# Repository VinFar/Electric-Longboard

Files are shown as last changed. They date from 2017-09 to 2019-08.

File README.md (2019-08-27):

# Self-Build electric mountain- and longboard with VESC and BLDC motor

##### Pressreport: https://www.fh-muenster.de/hochschule/aktuelles/pressemitteilungen.php?pmid=7254

This is a small Repo about my selfbuild electric mountain- and longboard, which I began to build in 2016 and 2019.
These are never ending projects, cause I will always come up with new ideas.

## Mountainboard
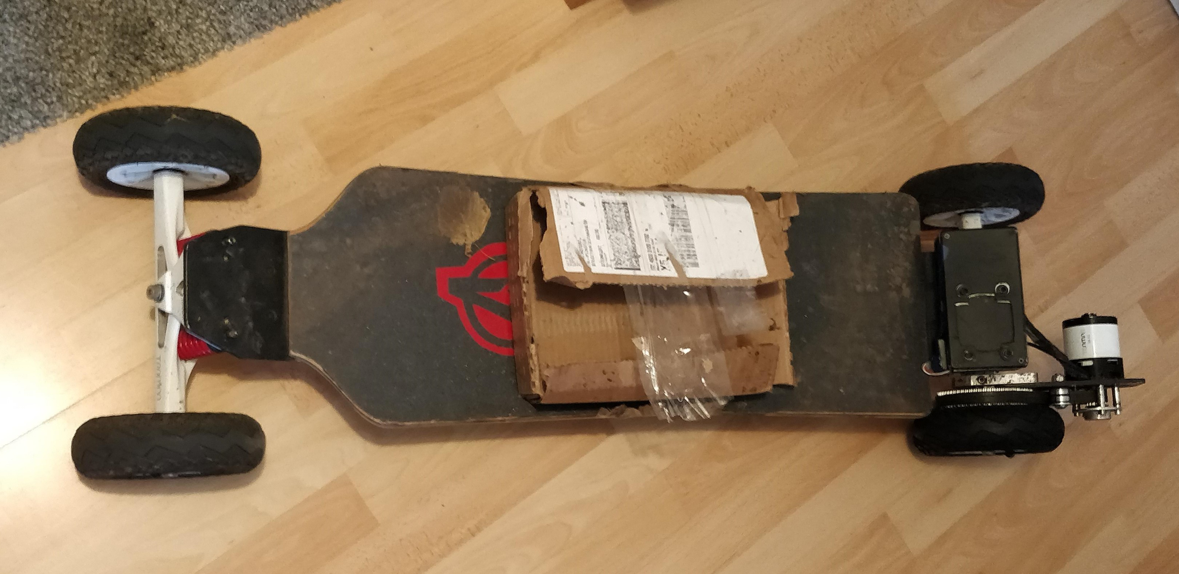
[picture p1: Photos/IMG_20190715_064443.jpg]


The longboard has been running very well for some time now and it's a lot of fun to ride.
But the small wheels (70mm diameter) are annoying and dangerous, because you have to pay attention to all medium sized stones and edges on the road, which will make the rides exhausting. Due of this and also because I was looking for a new challenge, I started building a mountainboard in May 2019.
This must have the following improvements:

- big pneumatic tires (at least 130mm in diameter)
- higher range (at least 30 km)
- newer version of the VESC
- USB-C PD charging capability
- 12S4P Li-ion battery pack

The first rough prototype of this is shown in the picture above. The box in the middle is a temporary battery box for testing.
At the moment (27.08.19) it has pneumatic tires with a diameter of 160mm, a range of about 35km  with ~600Wh 12S2P Lipos and VESC 6 with Bluetooth module.

Another thing that bothered me with the first longboard, was that I always had to take a 12V PSU and a Lipo charger with me in order to charge the batteries.
So for the Mountainboard i came up with the idea of charging the batteries over a [60W - 100W USB C Power Delivery power supply](https://www.voelkner.de/products/1055964/LVSUN-80W-USB-C-QC3.0-LS-Q5U-PD-USB-Ladestation-Steckdose-Ausgangsstrom-max.-17000mA-5-x-USB-3.0-Buchse-A-USB-C-Buchse-USB.h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). On awesome feature of USB C is that it can deliver up to [100W over the small USB-C plug](https://en.wikipedia.org/wiki/USB-C#USB_Power_Delivery) (20V and 5A).
I want to use this in combination with a [50V boost converter](https://www.droking.com/dc-boost-converter-power-supply-module-adjustable-regulator-dc-10v-40v-to-10-50v-6a-step-up-converter-dc-12v-24v-cc-cv-voltage-regulator-boar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) and the open source BMS [DieBieMS](https://github.com/DieBieEngineering/DieBieMS) to have to ability to charge it on every socket.

The 12S4P Li-ion battery pack will be mounted beneath the deck in the form of a modular system, which is shown below.
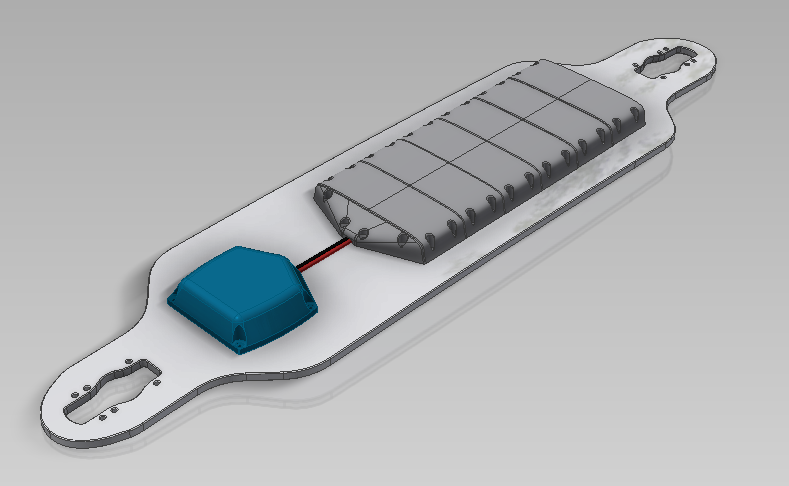
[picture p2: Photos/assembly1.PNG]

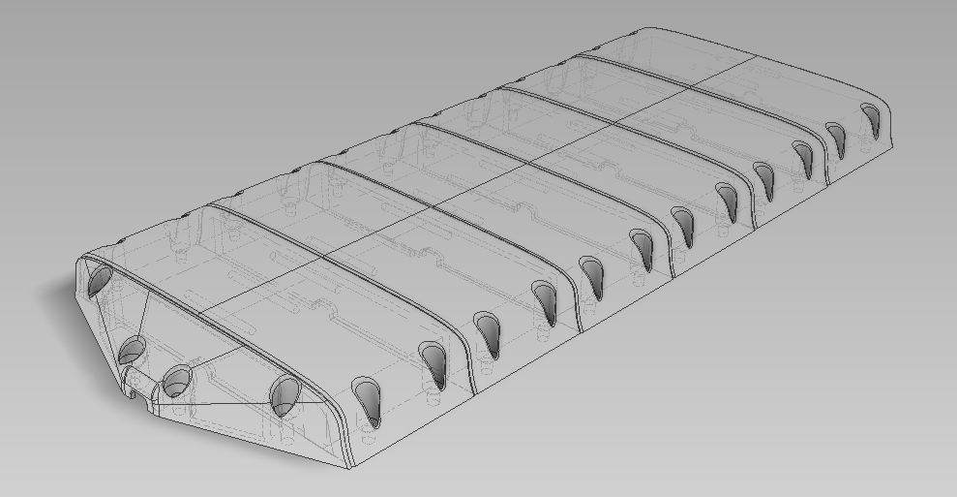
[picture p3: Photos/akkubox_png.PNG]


In every battery tray there is space for a 2S3P/3S2P/1S6P/6S1P battery pack. This trays are then connected in series to raise the voltage and/or the capacity. The BMS, the converter and the VESC will sit in the blue housing at the end of the mountainboard.

The first test ride with the this board were awesome. It runs so much better on all terrains, so you don't have to worry about stones and bumps any more. Even on uneven tracks like in a forest or on grass it runs good.

In the future I will get a second motor to also drive the second tire and to have more torque (at the moment the power is ok, but could definitly be more).

## Longboard
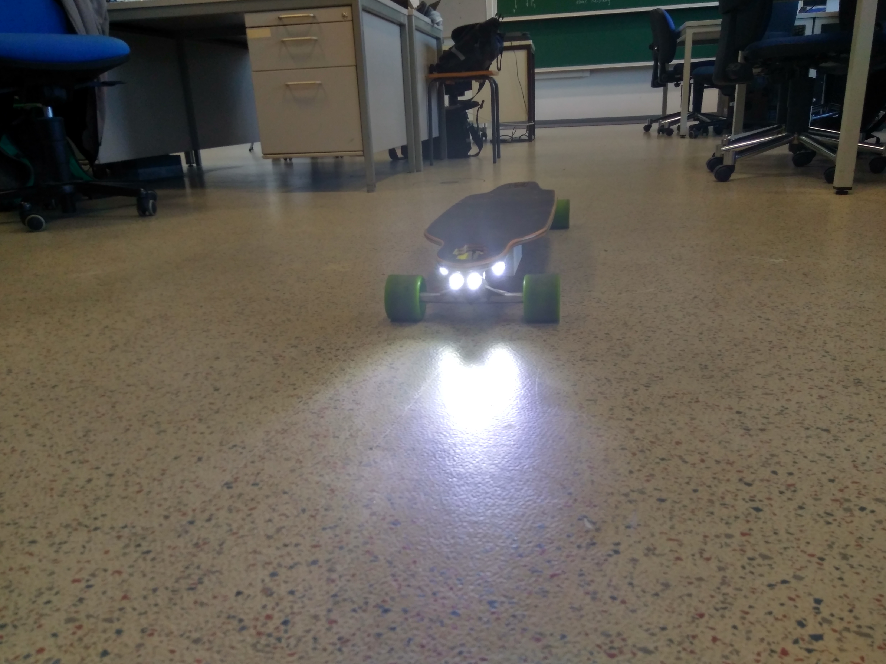
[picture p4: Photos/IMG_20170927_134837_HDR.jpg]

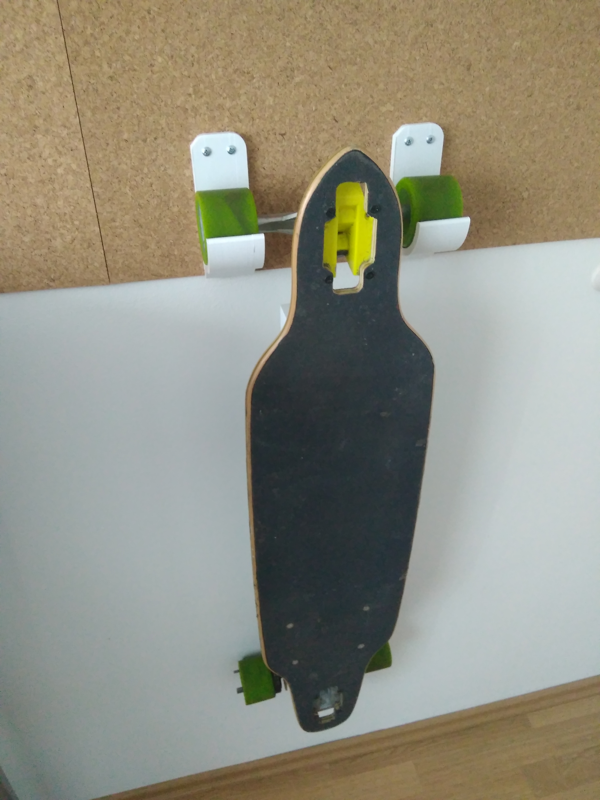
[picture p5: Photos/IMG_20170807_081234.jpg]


#### ToDo's:
* Backlight with Brakelight
* [Failsafe Function with Rubberband](https://www.svb.de/de/sicherheits-schalter.html)
  -If you jump off the board, let the board make a full brake

#### Not-ToDo's (already done):
* Cleaner Cable Managment
  - XT-60 Box
* Built cases
  - VESC-Case
  - CC converter case
  - Battery case
* Better Motorplate
  - 3mm stainless steel
* Changed Transmitter Case
  - [Baby Buffalo](https://www.thingiverse.com/thing:1810252)
* [LED-Headlight](https://github.com/VinFar/Electric-Longboard/tree/master/Inventor%20Files/LED-Headlight)

For the motor I choose [this BLDC Motor](http://www.hellray.de/shop/#!/eSk8-de-Motor-esk8-6354-200kV-2-2KW-mit-Sensoren/p/65758944/category=15255004).
It is recommend for 2,2kW, but due to sufficient cooling it can be powered with up to ~3.2kW (~40V with 80A max, efficiency ignored).

For the ESC I went with the aweseome [VESC 4](http://vedder.se/2015/01/vesc-open-source-esc/).

As Batteries two 5s LiPos are used, which are connected in series to get a voltage of up to 42V.
They have 5Ah each, so a total energy of around 200Wh can be consumed, which is enough 10-15 km depending on the driving speed.

For the Communication between the VESC and the driver, I got a [GT2B](https://www.google.de/search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), which i then put into a [3D printed housing](https://www.thingiverse.com/thing:1810252) to get a small and ergonomic remote.

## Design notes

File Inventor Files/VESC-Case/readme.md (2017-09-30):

# Nice looking Case for VESC and other Components

This is is stylish Case for the VESC and other Compoments like Capacitors, Buck-Converters,Receiver etc...
It is about 35mm in height, therefore it looks very slim under the board.
For this Case I also scanned the Outlines from the bottom part of the Longboard, to make it look like a part of the Board.

I uploaded a [Clean Version](https://github.com/VinFar/Electric-Longboard/blob/master/Inventor%20Files/VESC-Case/Clean_Version_2.stl), in which is only the Case without any cutouts or holes, so you can edit it for yourself.
Also there is a ["USB Version"](https://github.com/VinFar/Electric-Longboard/blob/master/Inventor%20Files/VESC-Case/USB_Version_2.stl),
where i made some cutouts and holes for switches, Powercables, USB-Output etc...

Clean Version(no cutouts): [Clean_Version_2.stl](https://github.com/VinFar/Electric-Longboard/blob/master/Inventor%20Files/VESC-Case/Clean_Version_2.stl)

USB Version(with cutouts): [USB_Version_2.stl](https://github.com/VinFar/Electric-Longboard/blob/master/Inventor%20Files/VESC-Case/USB_Version_2.stl)

I think I will make a Version 3 in the near future with bigger dimensions and a more racy design.

-----

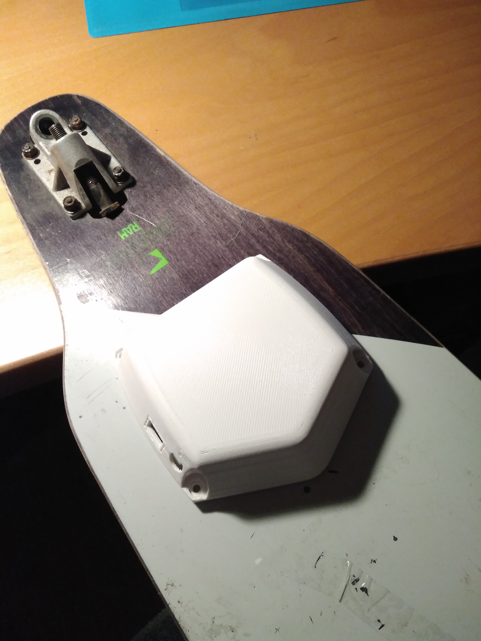
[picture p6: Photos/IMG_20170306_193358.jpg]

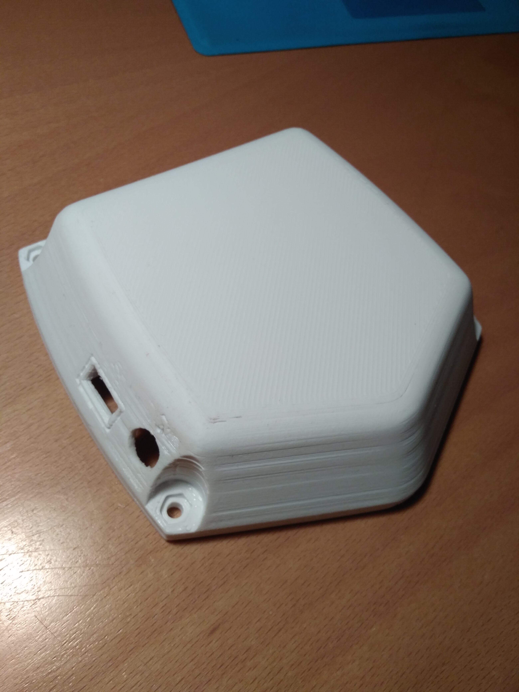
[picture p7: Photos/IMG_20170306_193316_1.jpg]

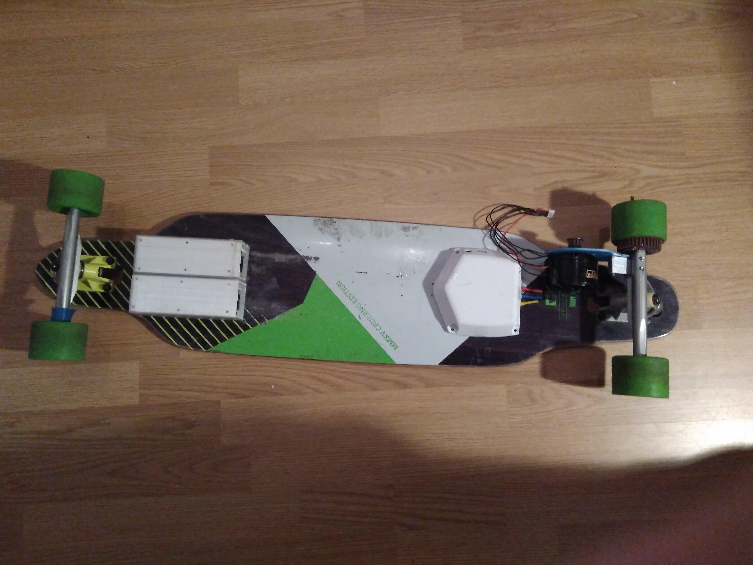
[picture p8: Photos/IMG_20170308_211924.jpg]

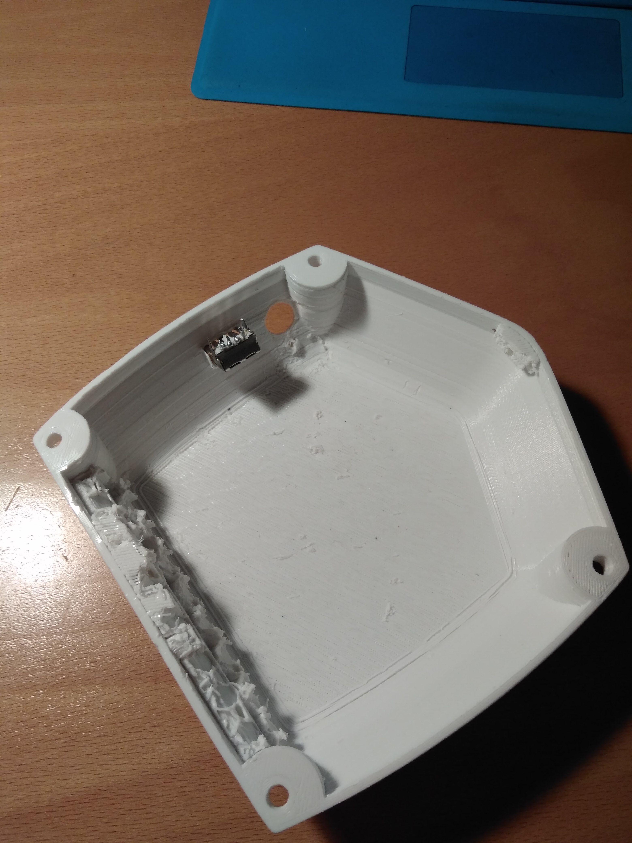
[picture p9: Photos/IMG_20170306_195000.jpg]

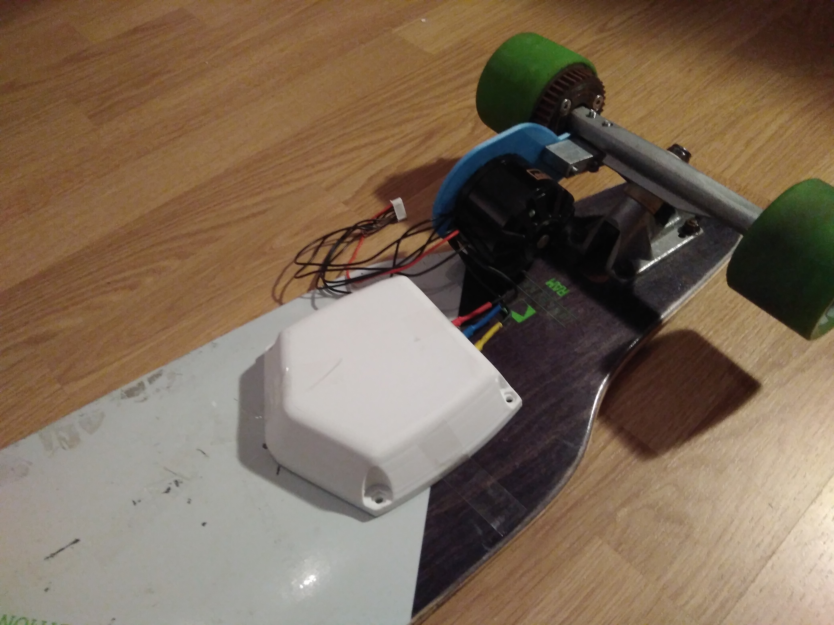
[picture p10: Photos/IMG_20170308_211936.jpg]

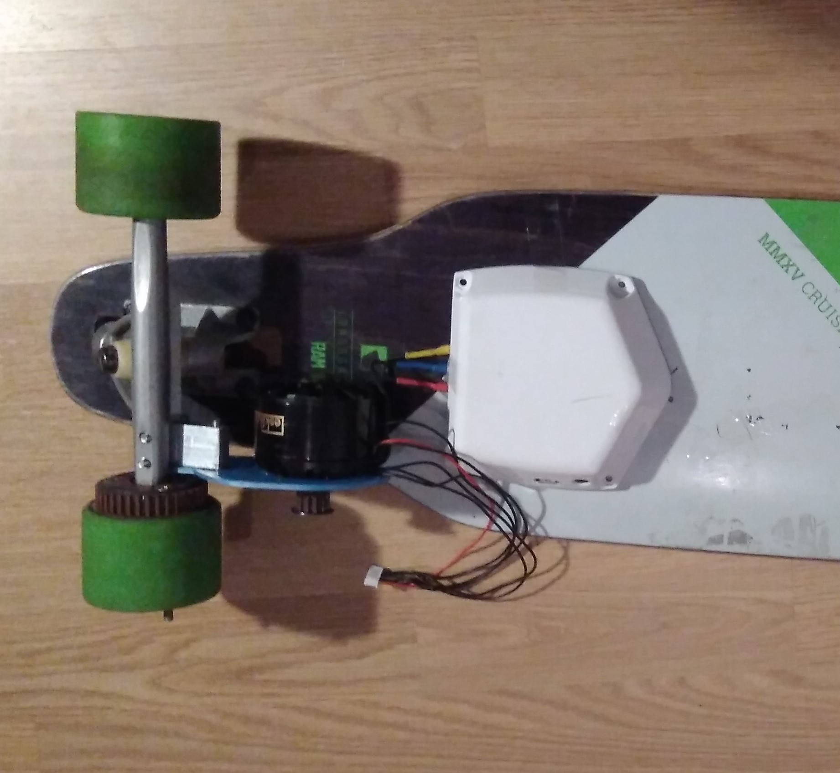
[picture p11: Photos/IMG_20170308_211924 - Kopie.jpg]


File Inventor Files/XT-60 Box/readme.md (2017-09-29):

# A small Case for two XT60 Male-Connecters

#### This is Case for two XT60 Connectors, which is placed in front of the Lipo Cases. Now I have a firm place to connect the batteries.
Also it gives a much cleaner look.

I have glued the Connecters with superglue into place and connected the batteries with copperwire and much solder.

Also I put the Mosfet for the LED Headlight in this case.

`Version2: Added a cage around the XT60 Connectors`

STL-Files:

[Version 1](https://github.com/VinFar/Electric-Longboard/blob/master/Inventor%20Files/XT-60%20Box/V1.0.stl)

[Version 2](https://github.com/VinFar/Electric-Longboard/blob/master/Inventor%20Files/XT-60%20Box/V2.0.stl)

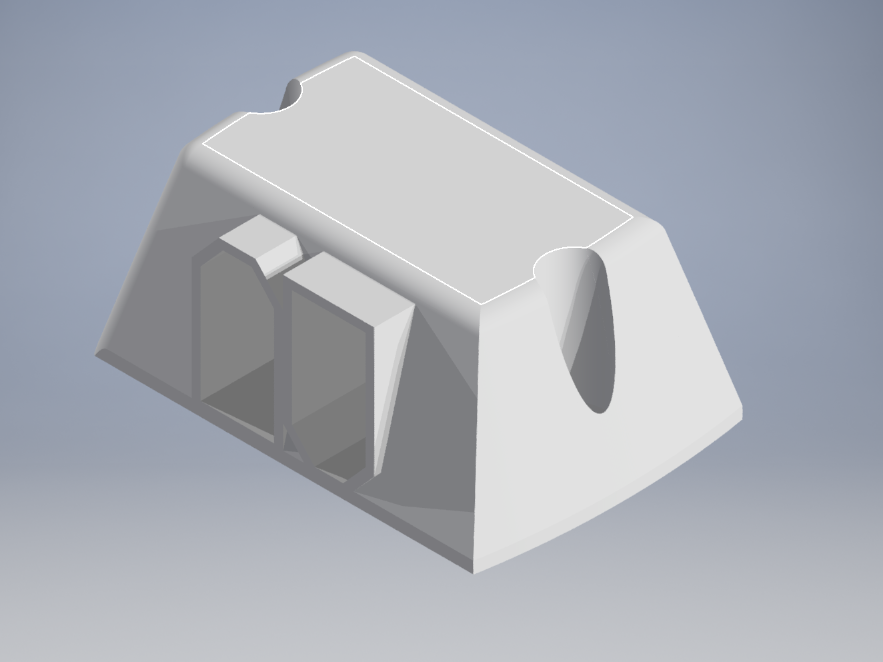
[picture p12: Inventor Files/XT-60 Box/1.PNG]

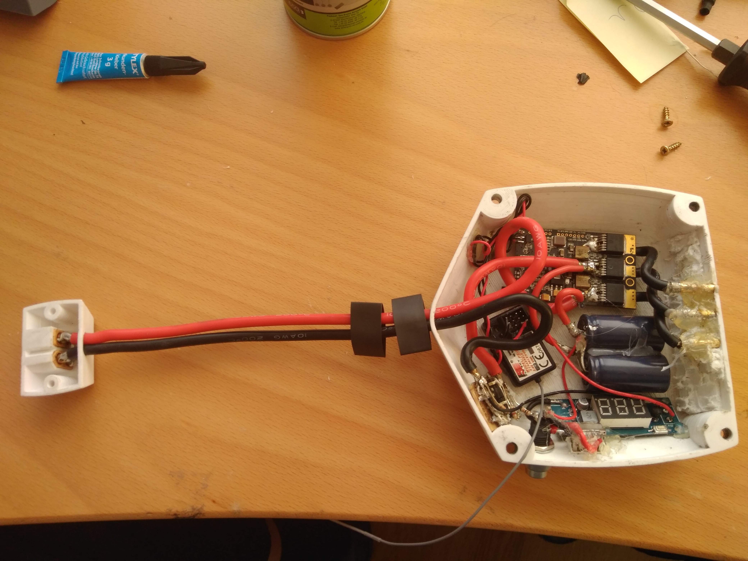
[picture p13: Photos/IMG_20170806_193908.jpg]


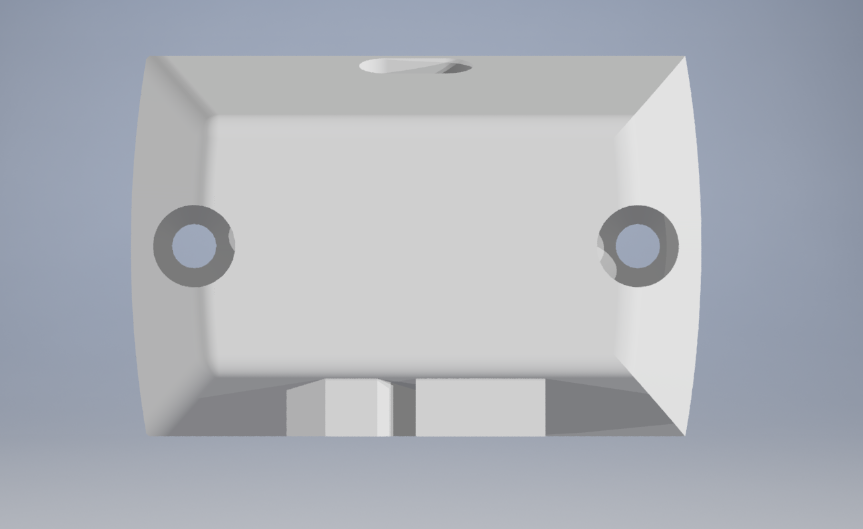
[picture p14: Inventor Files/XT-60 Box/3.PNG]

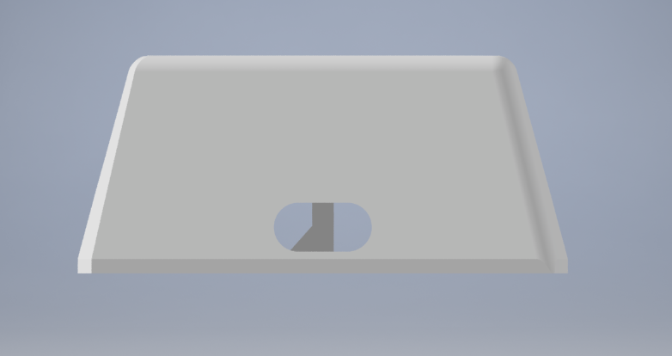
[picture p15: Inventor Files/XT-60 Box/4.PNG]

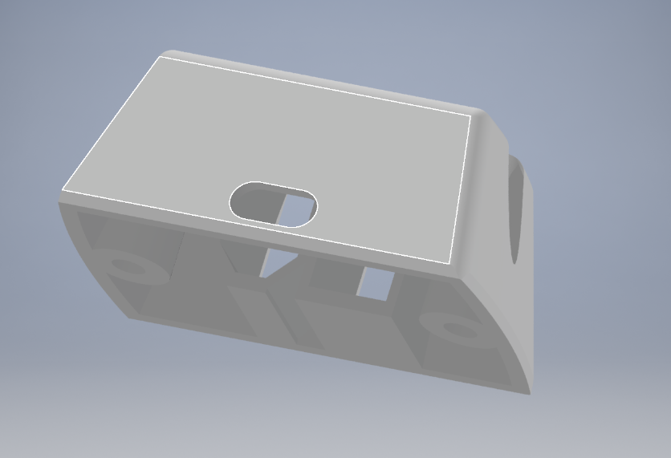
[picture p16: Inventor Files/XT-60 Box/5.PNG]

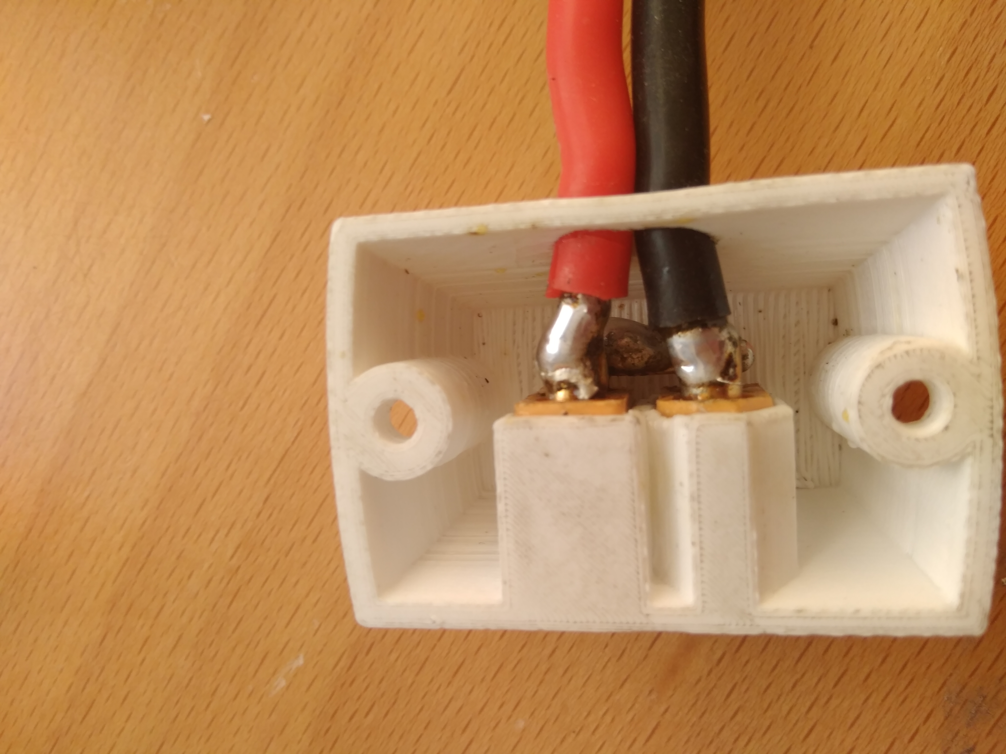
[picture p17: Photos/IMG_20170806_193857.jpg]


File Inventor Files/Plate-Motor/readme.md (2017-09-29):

# Simple Motorplate for with 21mm bolt circle.

This is a simple Plate to screw the Motor to the Longboard. I cut it from 3mm stainlesss steel with CNC Laser.

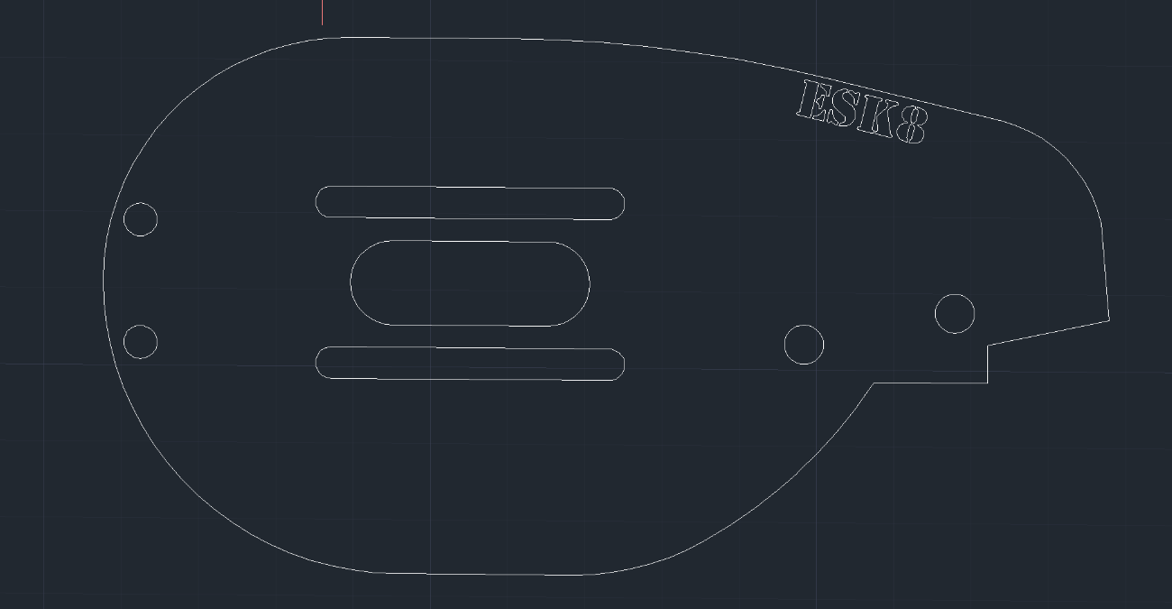
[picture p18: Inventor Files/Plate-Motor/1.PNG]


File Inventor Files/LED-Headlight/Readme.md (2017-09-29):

# LED-Headlight for Electric Longboard

#### I wanted to solve Problem that I couldn't properly watcht the road when it is dark outside. So I build this LED-Headlight,
#### which perfectly fits beneath the front of the Board



I scanned the outline of the bottom layer and converted it into a 2D Frame.
Then i took [this](http://www.ebay.de/itm/LED-Linse-Optik-Reflektor-10-Stck-Linsen-30-f%C3%BCr-1W-3W-5W-Power-LED-Leds-Lens/182454739604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) LED Lenses with an angle of 30° and made a 3D model where the Lenses fit in.
The front LEDs are facing 10° towards the ground and the two rear LEDs are facing 10° towards the ground and 10° towards the outside.
With this constellation i get a wider Lightarea.

`ToDo for Version 2:
    Put caps above the LEDs to prevend dazzling other traffic members!
`

I used normal 3W Power LEDs with a small additional heat sink. To drive the LED I took a [LM2596HV](http://www.ebay.de/itm/DC-DC-LM2596-HV-S-Buck-Constant-Current-Voltage-CC-CV-Step-Down-Module-60V-3A-/232457602919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) CC Buck Converter.
For my requirements it was necessary to use the HV version of the Convert, because of the relatively High Voltage of 42V from the Lipo.
Also it is recommend to use the CC Version, because such Power LEDs has to be driven by a constant current and not a constant voltage!
For the Converter i created an external small case which sits in front of the Battery Cases.

To switch the Headlights on and off i used the unused third channel of the Remote Control.
I used a simply microcontroller, wich permanently monitors the PWM Signal of the third Channel.
The controller switches a simple Mosfet switch, which switches the High side.

The Headlight is [Version1.stl](https://github.com/VinFar/Electric-Longboard/blob/master/Inventor%20Files/LED-Headlight/Version1.stl)

The Converter Case is [Stromquelle_gehäuse.stl](https://github.com/VinFar/Electric-Longboard/blob/master/Inventor%20Files/LED-Headlight/Stromquelle_geh%C3%A4use.stl)

A timelapse Video of the 3D modeling phase is here(click! this is only a gif):
Demo CountPages alpha (https://youtu.be/nJyjoMh7dLY)

A timelapse Video of the 3D Printing is here(click! this is only a gif):
Demo CountPages alpha (https://youtu.be/3woWbC7GaZc)

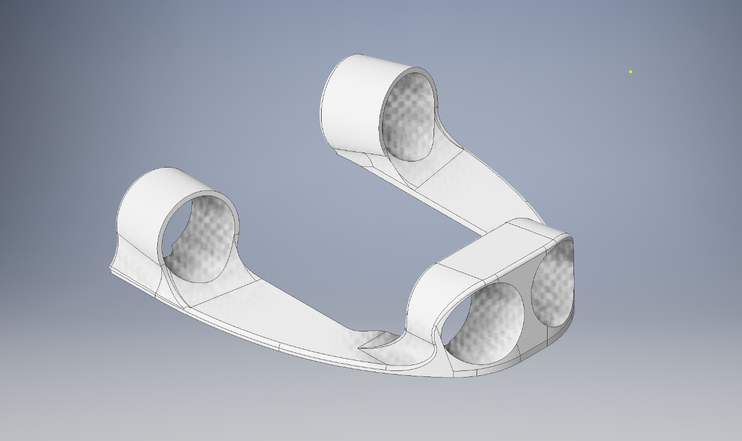
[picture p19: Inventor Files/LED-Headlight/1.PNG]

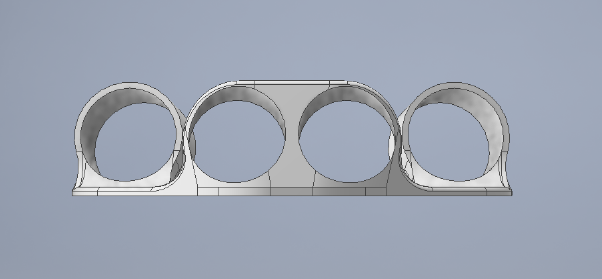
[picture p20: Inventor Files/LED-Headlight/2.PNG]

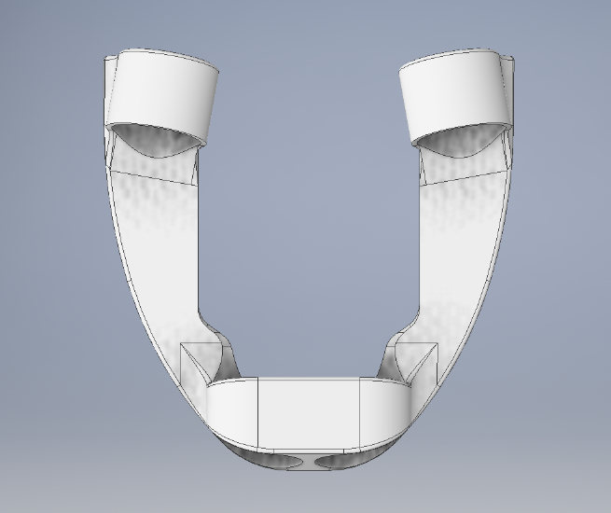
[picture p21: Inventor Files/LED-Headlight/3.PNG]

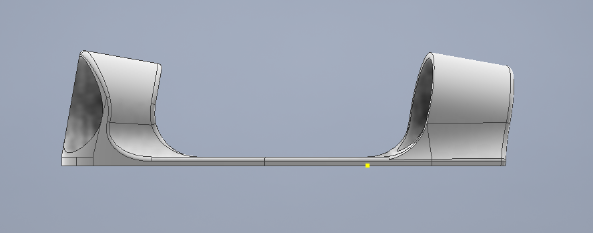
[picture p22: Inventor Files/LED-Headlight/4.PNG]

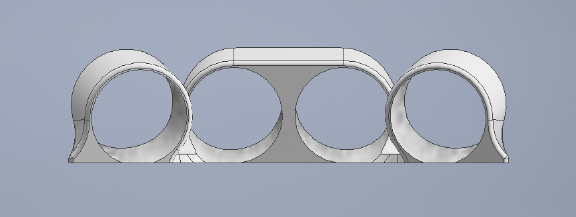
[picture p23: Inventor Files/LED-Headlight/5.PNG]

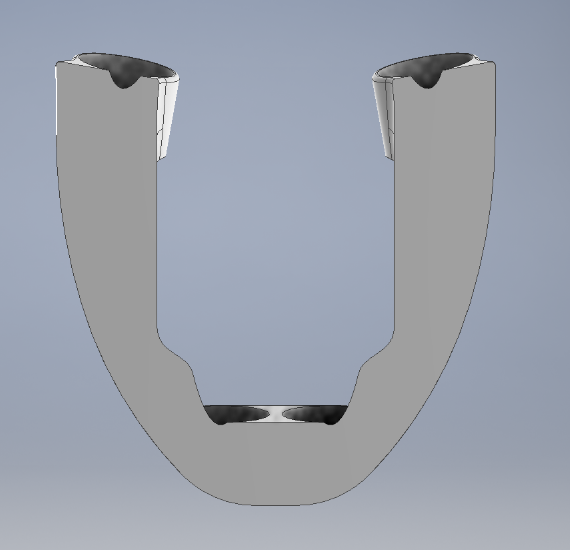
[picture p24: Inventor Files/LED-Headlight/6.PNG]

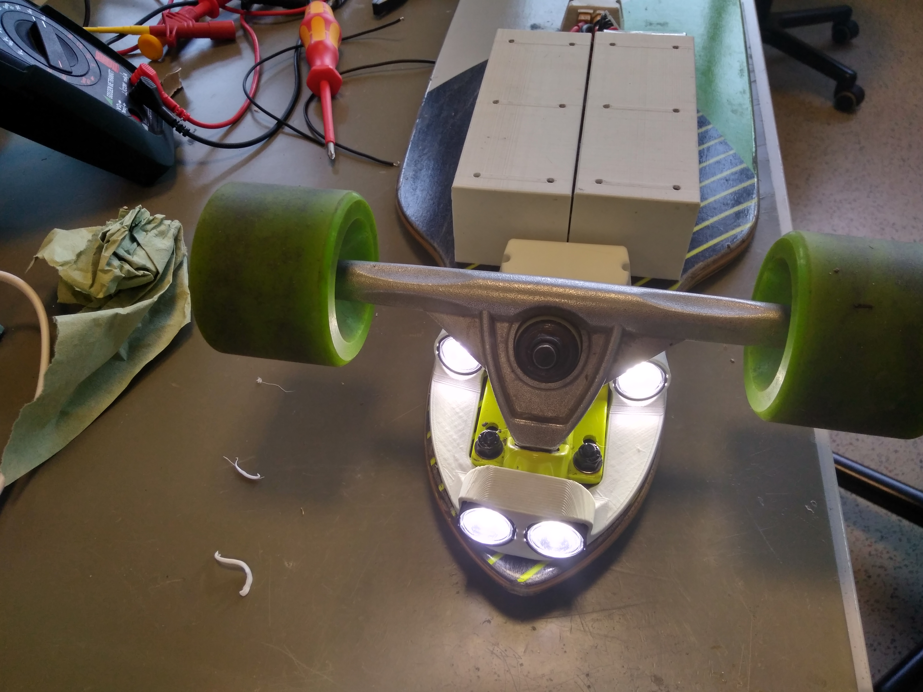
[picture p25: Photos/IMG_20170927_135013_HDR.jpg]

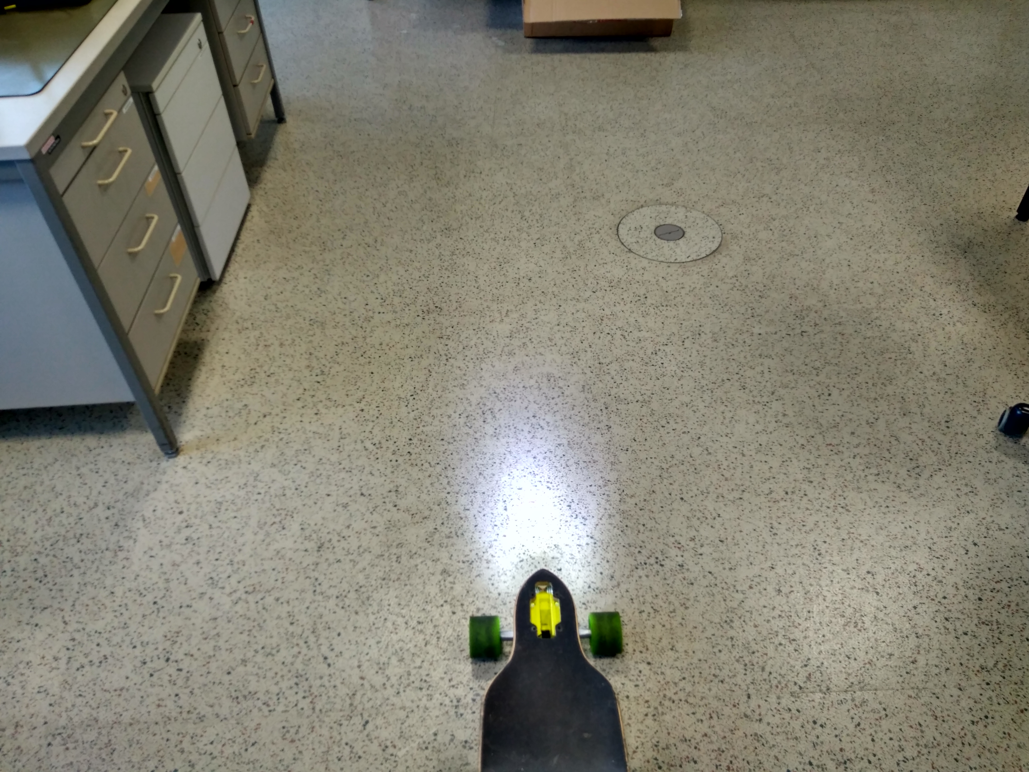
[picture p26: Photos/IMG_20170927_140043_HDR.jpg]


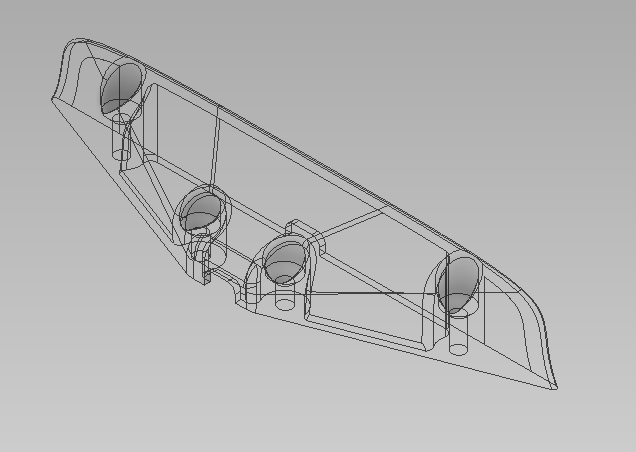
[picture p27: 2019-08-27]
Photos/front3.PNG

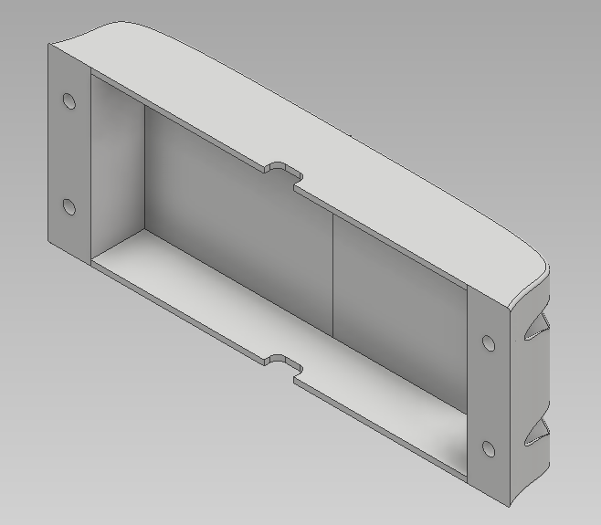
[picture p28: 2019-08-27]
Photos/box1.PNG

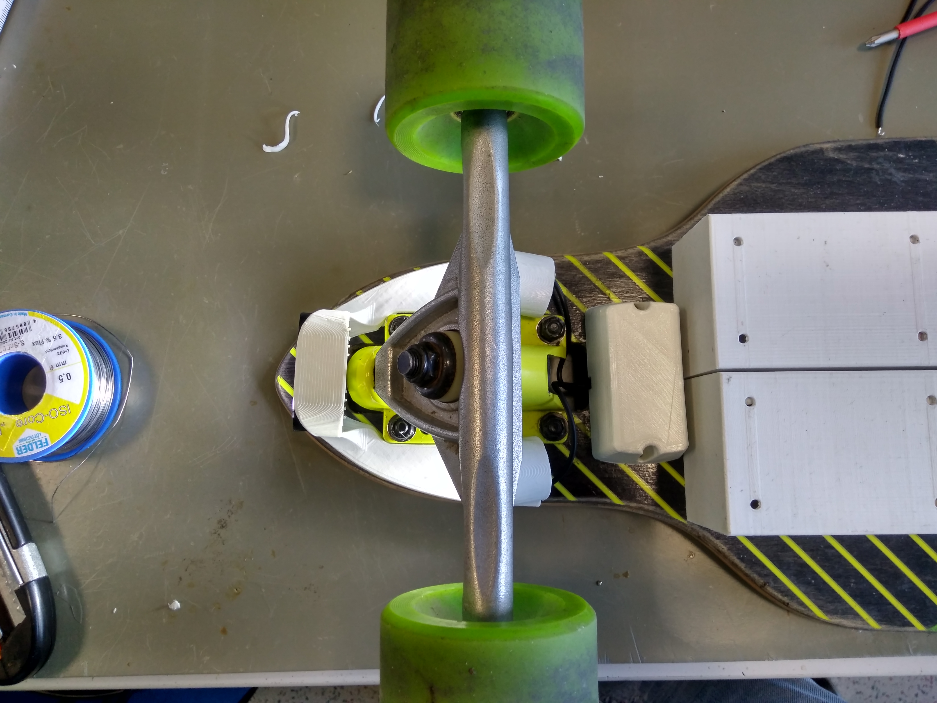
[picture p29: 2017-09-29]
Photos/IMG_20170927_135003_HDR.jpg

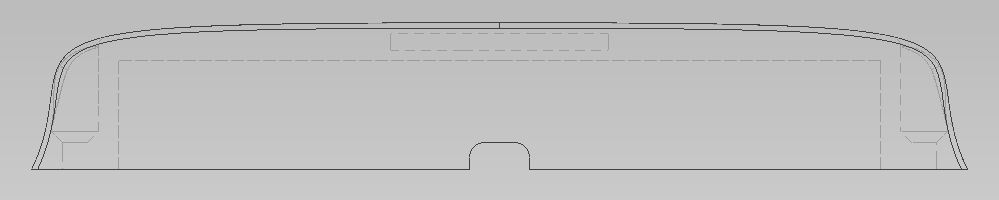
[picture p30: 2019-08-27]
Photos/box4.PNG

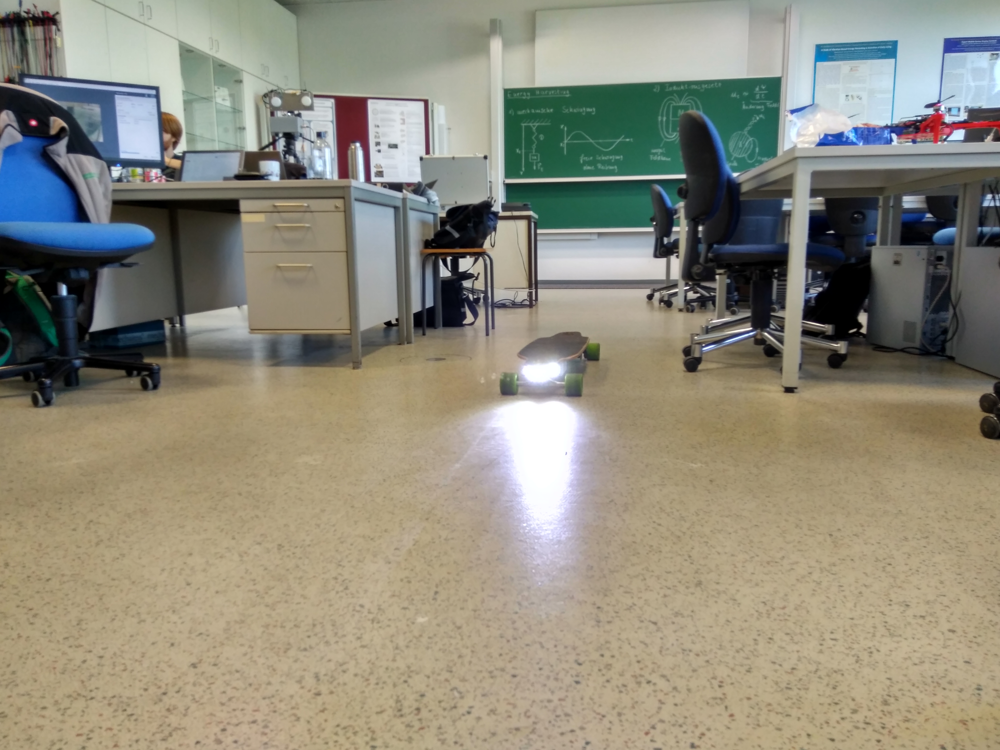
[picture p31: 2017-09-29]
Photos/IMG_20170927_133459_HDR.jpg

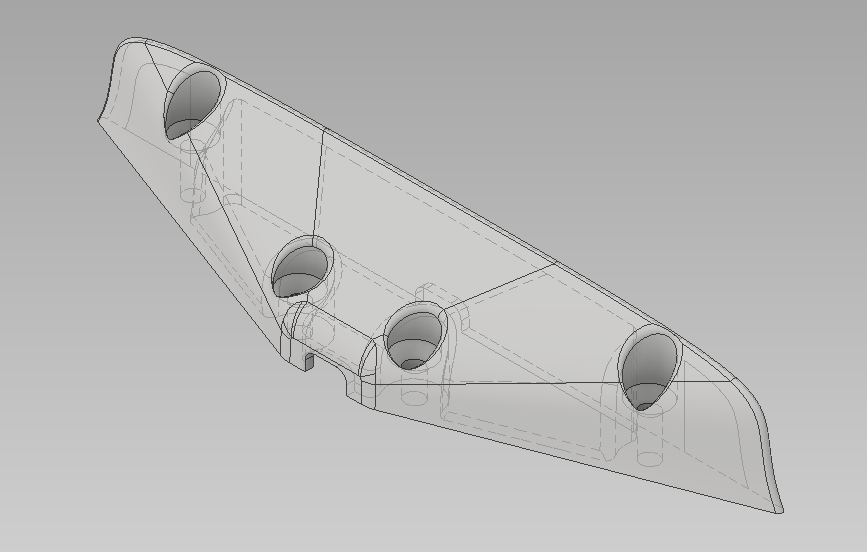
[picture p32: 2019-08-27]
Photos/front.PNG

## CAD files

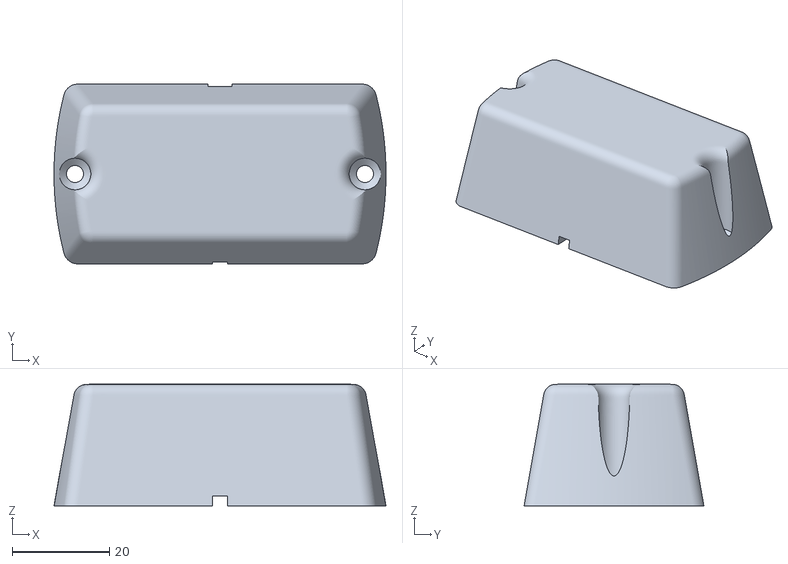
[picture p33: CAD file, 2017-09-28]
Inventor Files/LED-Headlight/Stromquelle_gehäuse.stl
68.3 x 37.0 x 25.0

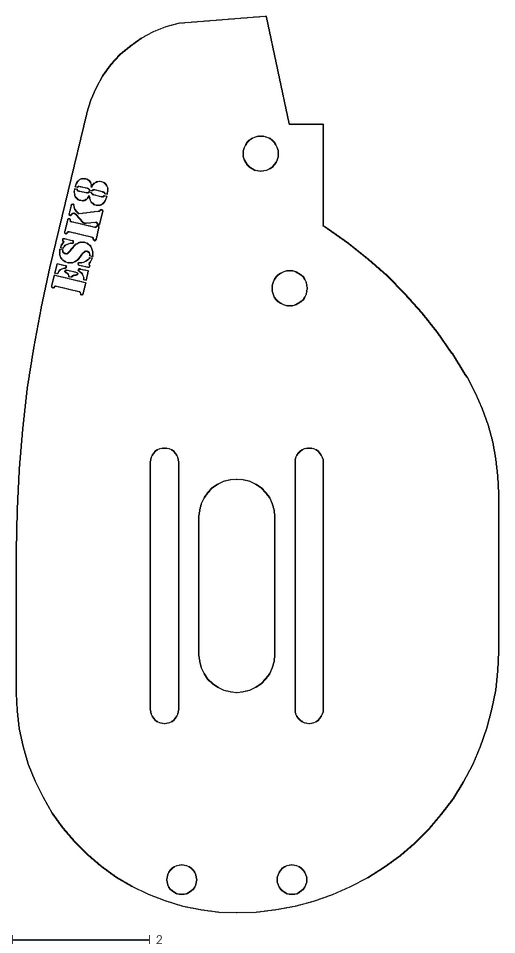
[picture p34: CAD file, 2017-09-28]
Inventor Files/Plate-Motor/motorplate.dxf
7.00 x 13.0

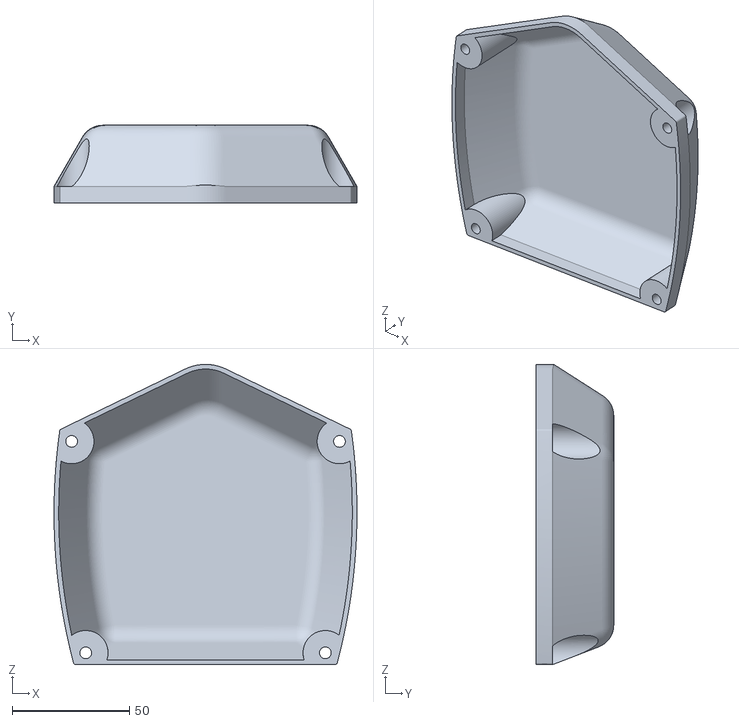
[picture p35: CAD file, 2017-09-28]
Inventor Files/VESC-Case/Clean_Version_2.stl
129.0 x 33.0 x 127.8

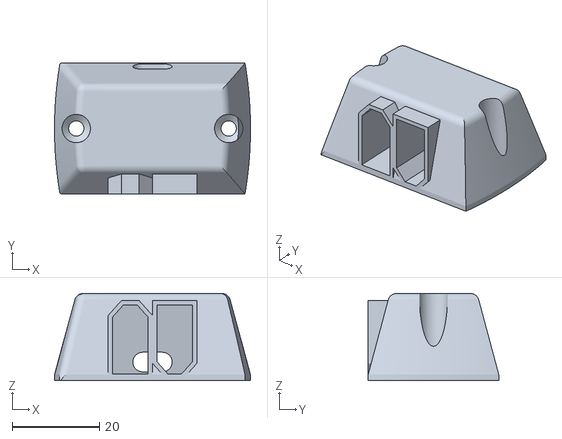
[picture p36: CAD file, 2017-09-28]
Inventor Files/XT-60 Box/V2.0.stl
45.0 x 30.0 x 20.0

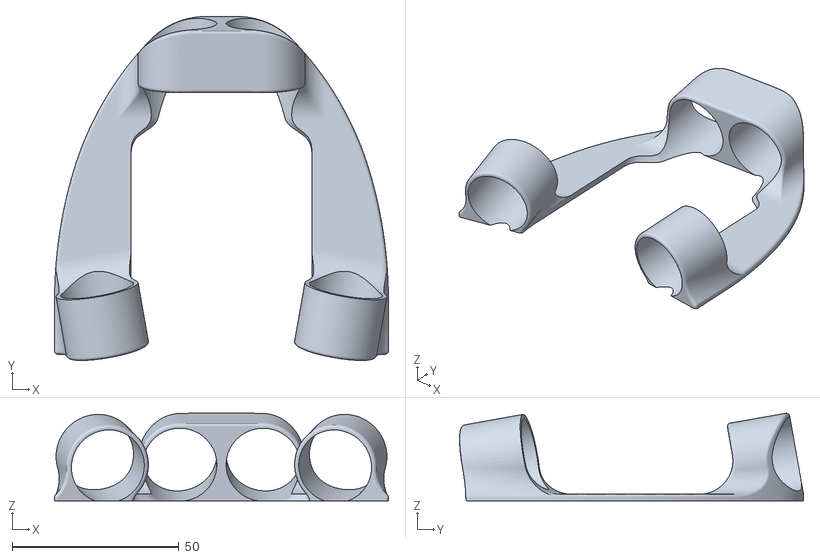
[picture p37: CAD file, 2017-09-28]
Inventor Files/LED-Headlight/Version1.stl
100.4 x 103.2 x 26.3

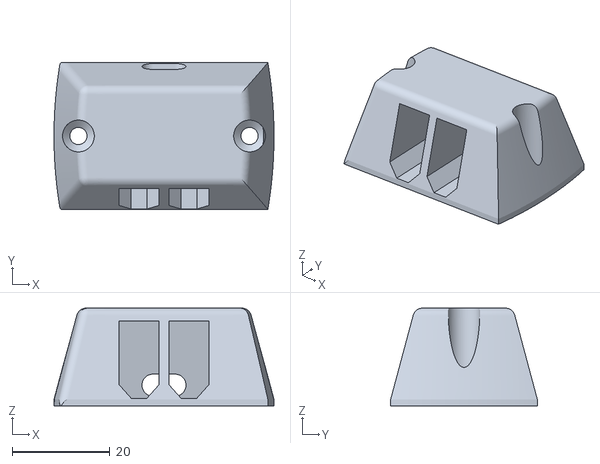
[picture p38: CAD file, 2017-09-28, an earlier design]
Inventor Files/XT-60 Box/V1.0.stl
45.0 x 30.0 x 20.0

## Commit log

2017-09-28 Initial Commit
    Added STL-Files and pictures
    [Clean_Version_2.stl, Stromquelle_gehäuse.stl, V1.0.stl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]
2017-09-29 added timelapse video
    Added a timelapse video from printing of the Headlight
2017-09-29 added timelapse gif of 3D Printer
2019-08-27 add: picture of mountainboard
2019-08-27 add: rotated picture of mountainboard
2019-08-27 add: pictures of battery box
2019-08-27 add: assembly overview
